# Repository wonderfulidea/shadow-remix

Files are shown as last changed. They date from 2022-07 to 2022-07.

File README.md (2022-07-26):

# Shadow Remix

Live demo at: [apps.wonderfulidea.co/shadow-remix/app/](https://apps.wonderfulidea.co/shadow-remix/app/)

- [Overview](#overview)
  - [Shadow Remix App](#shadow-remix-app)
  - [Online Gallery](#online-gallery)
  - [Gallery Admin Interface](#gallery-admin-interface)
  - [Arduino](#arduino)
  - [Repo Structure](#repo-structure)
- [Use](#use)
- [License](#license)
- [Hotkeys](#hotkeys)
- [Limitations](#limitations)
- [Parts List](#parts-list)
- [Schematics and PCB](#schematics-and-pcb)
- [Backend Setup](#backend-setup)
- [Serial Communication](#serial-communication)
- [Code](#code)
  - [Install nodejs and npm](#install-nodejs-and-npm)
  - [Compiling UI Library](#compiling-ui-library)
  - [Compiling Desktop App](#compiling-desktop-app)
  - [Adding Screensaver Animations](#adding-screensaver-animations)
  - [Compiling Gallery](#compiling-gallery)

## Overview

This project consists of a few pieces of code that interact with each other:

### Shadow Remix App

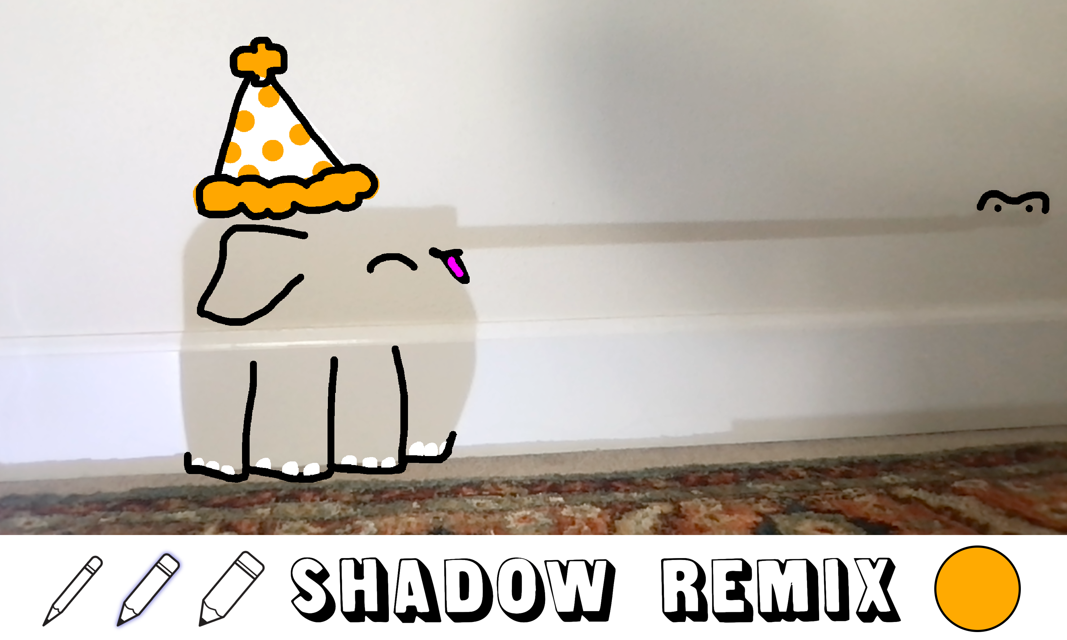
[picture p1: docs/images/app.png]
shadow remix app


The Shadow Remix drawing interface is available both as javascript code that runs in a web browser *or* as a compiled desktop app for Windows and Mac.  A live demo of the code is hosted at [apps.wonderfulidea.co/shadow-remix/app/](https://apps.wonderfulidea.co/shadow-remix/app/).

The browser-based drawing interface does not have the ability to upload photos to [our online gallery](https://apps.wonderfulidea.co/shadow-remix/gallery/) due to security issues (we don't want to let anyone on the internet upload photos to the gallery), but it does let users save images to their computers.

You will need to [compile your own copy of the desktop Shadow Remix drawing interface](#compiling-desktop-app) with credentials for editing your database.

### Online Gallery

shadow remix gallery

The gallery is a separate web app that displays approved photos drawn by visitors at the museum exhibition.  It has a feature where any new (unapproved) drawing made in the museum is shown for a brief period and then hidden until it is [approved by an admin](#gallery-admin-interface).

The gallery is currently hosted at [apps.wonderfulidea.co/shadow-remix/gallery/](https://apps.wonderfulidea.co/shadow-remix/gallery/).

### Gallery Admin Interface

shadow remix admin interface

The gallery admin interface is a private web app that displays saved photos drawn by visitors at the museum exhibition and allows an admin to approve them for public viewing.  You will need to [compile and host your own copy of the admin interface](#compiling-gallery) with credentials for editing your database.

### Arduino

The museum exhibit features a motorized shadow-making setup and a panel of button controls for easier interaction.  All the electronics for this exhibit are controlled by an [Arduino](https://www.arduino.cc/) which communicates via USB to the desktop app.

### Repo Structure

This repo consists of several subdirectories:

- [app](app) folder contains both a standalone browser-based application for shadow remix and the UI library code for connecting to a webcam, drawing to the screen, and saving images.
- [electron](electron) folder has code for compiling the desktop app with [Electron](https://www.electronjs.org/), it depends on the UI codebase located within the `app` folder.
- [gallery](gallery) folder has code for a publicly accessible gallery webpage showing images uploaded by users.
- [gallery-admin](gallery-admin) folder has code for a private admin interface for approving images.
- [arduino](arduino) folder contains arduino code for connecting hardware buttons to the app.

## Use

You need to compile your own Windows (64 and 32 bit) and Mac installers following the instructions for [compiling the desktop app](#compiling-desktop-app).  Once built, you should be able to install the app on any desktop setup.  These app is not signed and may require some additional steps to open:

- On Mac, hold down the control key and right click on the application icon, then select `Open`.  Confirm that you would like to open the application by an unidentified developer.  You should only need to do this the first time you run the application.  More info [here](https://support.apple.com/guide/mac-help/open-a-mac-app-from-an-unidentified-developer-mh40616/mac).

The first time you open the app, it will ask permission to access the webcam in a pop-up dialog.

## License

This work is distributed under an MIT license with exception to the "Lunch" font by Anthem Type.  See [Lunch Font](https://www.fontspace.com/lunch-font-f3679) for more details about licensing.

## Hotkeys

This app is primarily intended for use in a museum environment via a touchscreen and peripheral button controls.  If you have access to a keyboard or MakeyMakey, you can also use the following hotkeys:

- `ctrl/command` + `z` OR `d` to undo
- `ctrl/command` + `s` OR `a` to save image
- `backspace/delete` OR `g` to clear
- `c` brings up a dialog for selecting the webcam device
- `p` brings up a dialog for selecting the serial port (desktop app only)
- `v` saves your current drawing as an animated video (webm format).  Webm videos are large and difficult to play, but very fast to save – which is why we use them.  You can also use video editing software like Adobe Premiere to convert the video format.  Once you have the mp4s, you can [add them to the desktop app](#adding-screensaver-animations).
- `h` puts the app into screen saver mode (desktop app only).

## Limitations

- Currently, this app expects to receive webcam feeds in landscape orientation and renders out at the resolution specified in [app/src/constants.ts](app/src/constants.ts).  I've noticed that when mobile devices are in portrait mode, the returned width and height from `getUserMedia()` look like the stream is still in landscape.  I have not found a consistent way to correct this yet.

## Parts List

See [docs/Parts_List.md](docs/Parts_List.md) for a list of hardware we used for our exhibit.

## Schematics and PCB

See [docs/PCB.md](docs/PCB.md) for schematics and info about making circuit boards for the exhibit.

## Backend Setup

This app uses an AWS S3 bucket to store saved images in the cloud.  The saved images can be viewed through a webpage at [apps.wonderfulidea.co/shadow-remix/gallery/](https://apps.wonderfulidea.co/shadow-remix/gallery/).  Info about configuring the AWS Backend can be found at [docs/Backend_Setup.md](docs/Backend_Setup.md).

## Serial Communication

The serial communication protocol between the desktop app and Arduino is described in [docs/Serial_Communication.md](docs/Serial_Communication.md).  All arduino code can be found in the [arduino](arduino) folder.

## Code

### Install nodejs and npm

Before you compile any part of the code, you will need to [install nodejs and npm](https://docs.npmjs.com/downloading-and-installing-node-js-and-npm) on your machine.  All compilation steps are done through the command line.

### Compiling UI Library

This repo comes with a pre-built version of the UI library, located at [app/dist/ui.js](app/dist/ui.js).  This library should be fine as is for most cases.  **If you do not plan to modify the UI code, skip to the [next section](#compiling-desktop-app).**

If you want to change the available colors, line thicknesses, and other aspects of the UI, you can make those edits within
[app/src/constants.ts](app/src/constants.ts).

If you want to change the hotkeys, you can make those edits within
[app/src/hotkeys.ts](app/src/hotkeys.ts).

After make changes to the UI code you need to compile the `app/src/` folder to `app/dist/` using the following commands:

First, [install nodejs and npm](#install-nodejs-and-npm).

In the terminal, navigate to the `app` directory:
```sh
cd app
```

Install all dependencies:
```sh
npm install
```

Compile with [Webpack](https://webpack.js.org/):
```sh
npm run build
```

You can also start a development server at [localhost:8080/](http://localhost:8080/) using the following command:
```sh
npm run start
```

### Compiling Desktop App

The javascript code in this repo is compiled with [Electron](https://www.electronjs.org/) so that it can be run as a desktop app (rather than in a web browser).

You will need to compile your own desktop app after following the steps to [set up an AWS bucket and permissions](docs/Backend_Setup.md) and create an `.env` file with your access keys.  If make changes to the UI library in the `app` directory, you will need to [compile it first](#compiling-ui-library) before compiling a new copy of the desktop app.

If you want to change things about the app's functionality (e.g. wait time before showing the screensaver, or which buttons map to which functions) you can make those edits within
[electron/src/constants.ts](electron/src/constants.ts).

To compile for Windows and Mac:

First, [install nodejs and npm](#install-nodejs-and-npm).

In the terminal, navigate to the `electron` directory:
```sh
cd electron
```

Install all dependencies:
```sh
npm install
```

To compile for Windows and Mac:
```sh
npm run build
```

Once complete, builds are located in the `electron/build` folder.  The `shadow-remix Setup #.#.#.exe` installer should work on 32bit and 64 bit Windows machines, and the `shadow-remix-#.#.#.dmg` or `shadow-remix-#.#.#-mac.zip` files contain builds for Mac.

If you would like to compile for Linux, edit the following line in [electron/package.json](electron/package.json):

```json
"build": "npm run compile && electron-builder -mw",
```

change to:

```json
"build": "npm run compile && electron-builder -mwl",
```

Then run:

```sh
npm run build
```

Linux build has not been tested and may require additional configs, see the [electron-builder docs](https://www.electron.build/multi-platform-build.html) for more information.

If you want to make changes to the app's code, you can quickly test them by running a local development server:
```sh
npm run start
```
This will open an app window and begin running the new code automatically.

### Adding Screensaver Animations

The desktop app features a screensaver mode where you can show animations of previously drawn shadow-remixes if the station has remained inactive for a period of time.  To create the videos, draw a shadow remix and then hit the `v` key when you are done.  This will step through your entire drawing sequence and save out a video (it may be a little slow).  Using a video editor, convert the webm videos that are saved to your computer into mp4.

Next, you need to create a folder at `electron/animations/` and add several videos to this folder (with format mp4).  After making these changes you will need to recompile the app.  Alternatively, if you would like to change these videos (or add new ones) without recompiling the app, you can edit the contents of the `Resources/animations/` folder in the app's build and restart the app (on Mac, right click on the app's icon and select "Show Package Contents", on Windows right click on the app's icon and select "More > Open file location").  To be safe, use filenames without spaces for any animations you add to the app.

### Compiling Gallery

This repo comes with a pre-built version of our public gallery, located at [gallery/dist/](gallery/dist/) and currently hosted at XXXX.

In order to view your own images, you will need to recompile the gallery after [setting up your AWS bucket and permissions](docs/Backend_Setup.md) and creating a `.env` file with your access keys.

You can also edit some parameters of the gallery (e.g. how long images stay up, how often to refresh) at the top of [gallery/src/index.ts](gallery/src/index.ts).

Once complete, compile the `gallery/src/` folder to `gallery/dist/` using the following commands:

First, [install nodejs and npm](#install-nodejs-and-npm).

In the terminal, navigate to the `gallery` directory:
```sh
cd gallery
```

Install all dependencies:
```sh
npm install
```

Compile with [Webpack](https://webpack.js.org/):
```sh
npm run build
```

You can also start a development server at [localhost:8080/](http://localhost:8080/) using the following command:
```sh
npm run start
```

Note that you will also need to add `http://localhost:8080` to you list of Allowed Origins in the [AWS backend setup](https://github.com/amandaghassaei/shadow-remix/blob/main/docs/Backend_Setup.md#enable-cross-origin-requests).

Follow these same instructions to compile the gallery admin interface (located in the [gallery-admin](gallery-admin) folder).  Once compiled, the files inside [gallery-admin/dist/](gallery-admin/dist/) can be run locally or [hosted behind a password protected server](docs/Backend_Setup.md#hosting-private-admin-server) to allow admins to approve new image that are saved from the app.  **Do not post the compiled gallery-admin interface publicly because it contains your AWS secrete keys!!**  By default, all files in `gallery-admin/dist` (with the exception of index.html) should be ignored from git.

You can edit some parameters of the gallery admin interface (e.g. how often to refresh) at the top of [gallery-admin/src/index.ts](gallery-admin/src/index.ts).

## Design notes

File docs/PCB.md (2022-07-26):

# Printed Circuit Boards

This repo also includes design files for a CNC machined PCB that plugs directly into an Arduino, supports up to two motor drivers, and includes screw terminals for connecting to all switches/motors in the shadow remix station.

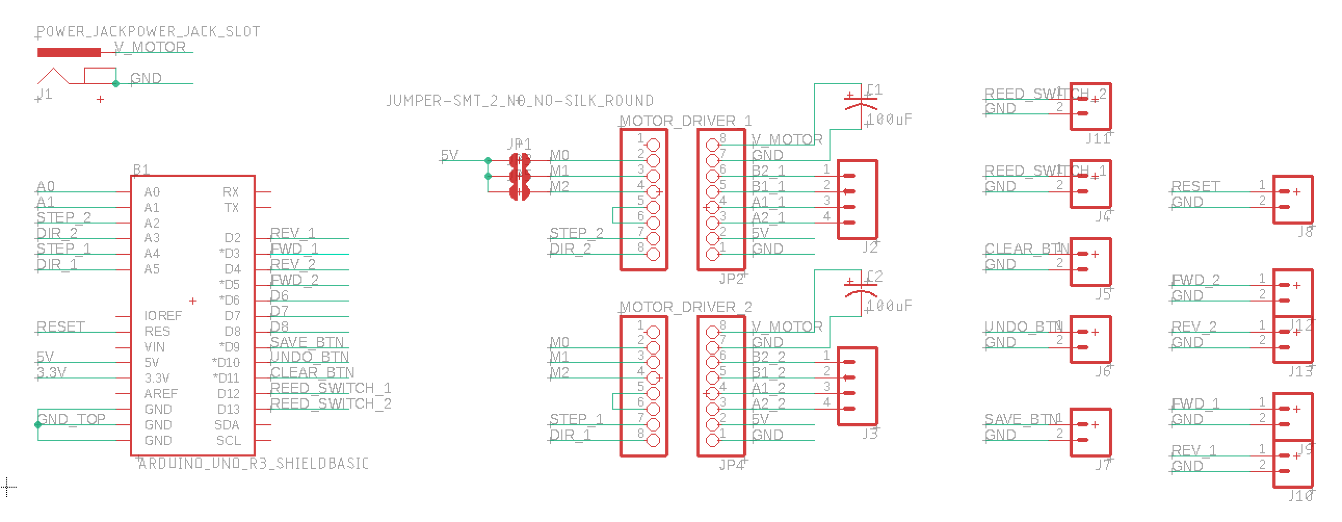
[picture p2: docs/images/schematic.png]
electronics schematic


## Wiring

See wiring diagram below:

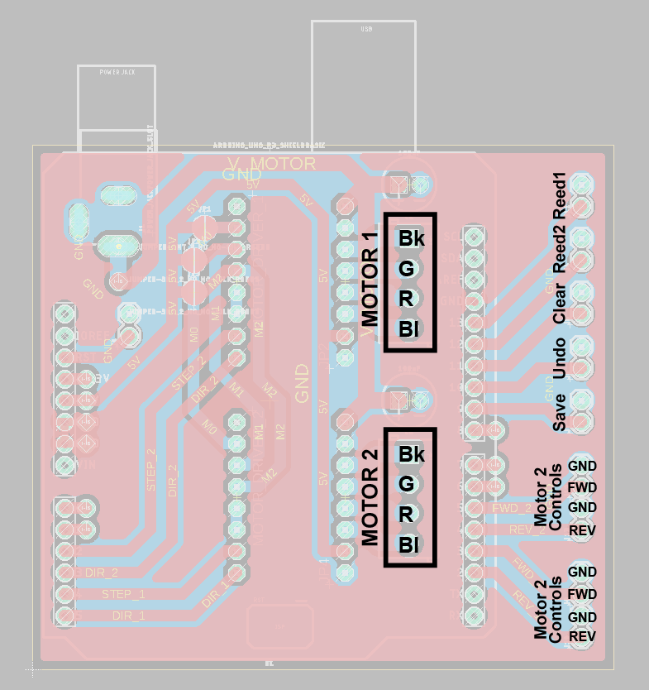
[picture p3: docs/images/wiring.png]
PCB wiring diagram


## Eagle Files

The PCB was designed in [Eagle](http://eagle.autodesk.com/) using components from the [Sparkfun](https://github.com/sparkfun/SparkFun-Eagle-Libraries) and [Adafruit](https://github.com/adafruit/Adafruit-Eagle-Library) Eagle libraries.  The design files are located in the [pcb](../pcb/) directory.

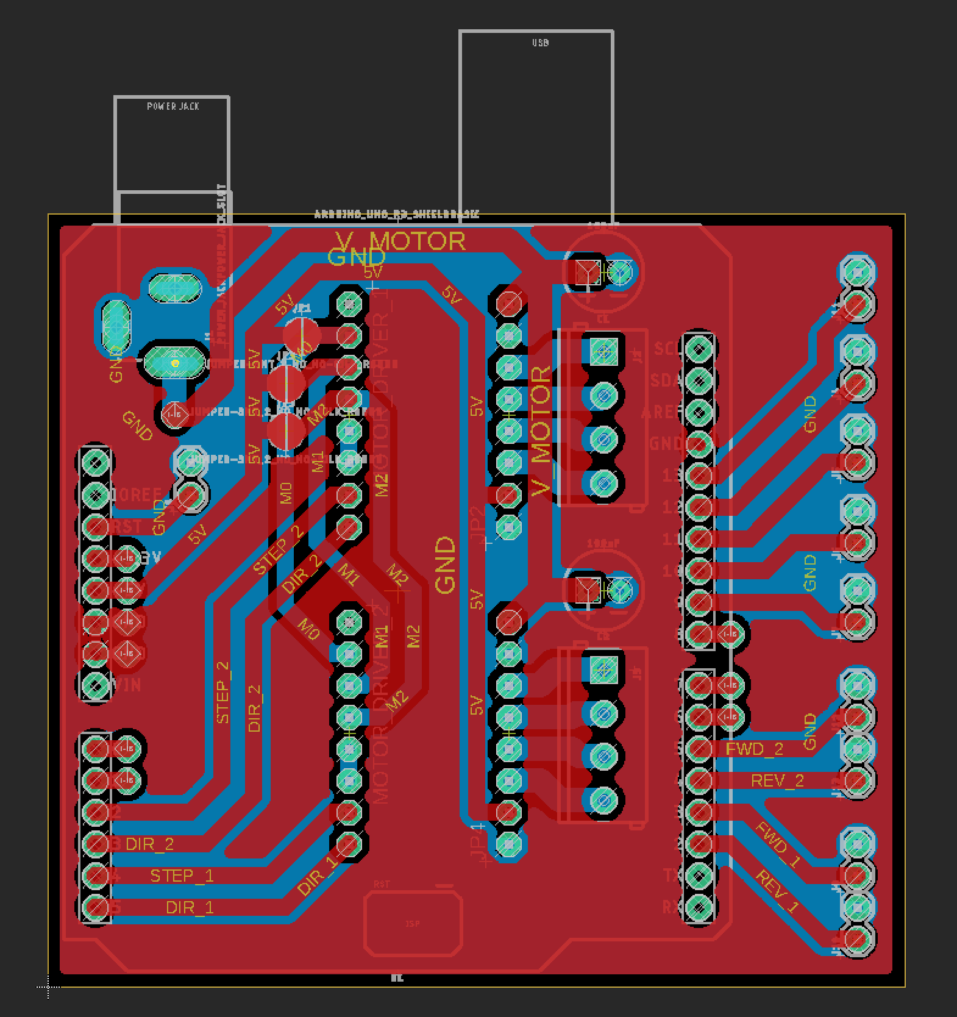
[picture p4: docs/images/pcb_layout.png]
electronics pcb layout


Features:

- Plugs directly into Arduino
- Up to two stepper motor drivers plug into PCB, supports [DRV8825](https://www.pololu.com/product/2133/pictures#lightbox-picture0J4233) and [A4988](https://www.pololu.com/product/1182/pictures#lightbox-picture0J10073) motor driver pinouts (and possibly others)
- Three solder jumpers to set stepper micro-stepping mode
- Two 100uF capacitors for smoothing power supply
- Unused Arduino IO pins have vias nearby for soldering headers later if needed
- 2.1mm jack for connecting motor power supply

Parts List:

(2x) A4988 Stepper Motor Driver [Amazon](https://www.amazon.com/HiLetgo-Stepstick-Stepper-Printer-Compatible/dp/B07BND65C8/)
(1x) through-hole male header pins 0.1" spacing [Digikey S1011EC-40-ND](https://www.digikey.com/en/products/detail/sullins-connector-solutions/PRPC040SAAN-RC/2775214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)  
(4x) through-hole female header pins 0.1" spacing [Digikey S7041-ND](https://www.digikey.com/en/products/detail/sullins-connector-solutions/PPPC081LFBN-RC/810180)  
(2x) 100uF Capacitor [Digikey 1572-1039-ND](https://www.digikey.com/en/products/detail/cornell-dubilier-illinois-capacitor/107CKE025MEM/5343969)  
(1x) 2.1mm jack through-hole [Digikey CP-002A-ND](https://www.digikey.com/en/products/detail/cui-devices/PJ-002A/96962?s=N4IgTCBcDaIMIAUC0AGFYCCSByAREAugL5A)  
(4x) 1x2 3.5mm screw terminal [Pololu 2444](https://www.pololu.com/product/2444)  
(6x) 1x2 0.1" screw terminal [Digikey A98333-ND](https://www.digikey.com/en/products/detail/te-connectivity-amp-connectors/282834-2/1150135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)  
(2x) 1x4 0.1" screw terminal [Digikey ED10563-ND](https://www.digikey.com/en/products/detail/on-shore-technology-inc/OSTVN04A150/1588864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)

## Milling PCB

Tools and Stock:

(1x) 1/64" diameter endmill [Carbide Depot CU 129974](http://www.carbidedepot.com/00156in-DIA-2FL-SE-AlTiN-164-P180142.aspx) - for cutting traces  
(1x) 1/32" dimeter endmill [Carbide Depot SGS 30398](http://www.carbidedepot.com/00312in-DIA-2FL-SE-132-AlTiN-COATED-P23340.aspx) - for cutting holes and board perimeter  
(1x) Double sided PCB blanks [Inventables 24201-06](https://www.inventables.com/technologies/circuit-board-blanks) - be sure to get FR1 blanks and not fiberglass-containing FR4  

In order to prepare the g-code for cutting the PCB, I exported the traces, holes, and board outline as PNG files from Eagle.  I made some changes to the design PNGs in Photoshop - adjustments to the hole sizes and offsets to allow enough clearance for the endmills.  The final PNGs I used are included in the [pcb](../pcb/) directory.  I used [mods.cba.mit.edu](https://mods.cba.mit.edu/) to generate gcode from the PNGs and added those to the [pcb](../pcb/) directory as well.

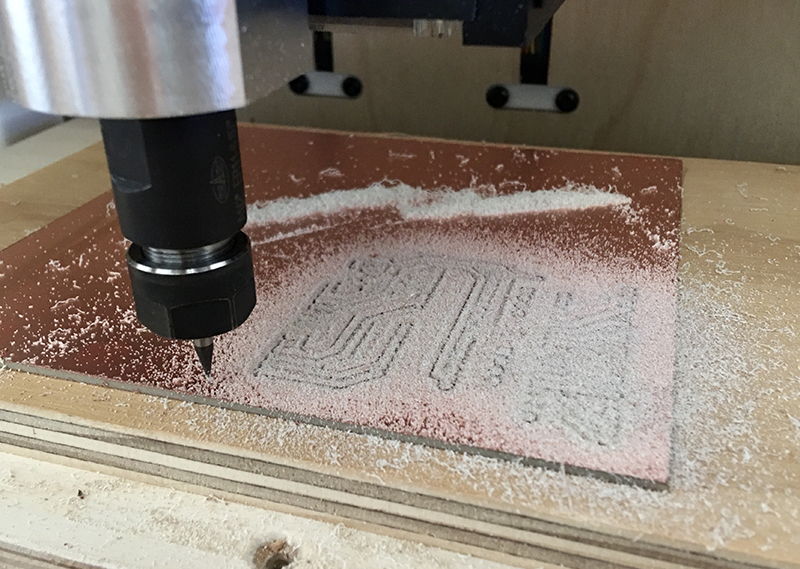
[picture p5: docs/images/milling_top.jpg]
milling trace of PCB


I used double sided tape to attach the PCB blank to a piece of spoilboard.  I zeroed to the bottom left corner of the stock and cut the holes first (1/32" endmill), then the top traces (1/64" endmill), then the outline (1/32" endmill).

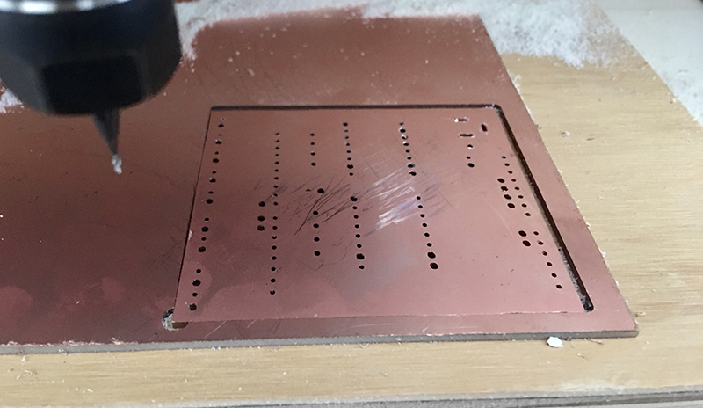
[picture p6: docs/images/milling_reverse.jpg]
aligning the reverse side of the PCB


I flipped the board and aligned it to the bottom left corner of the hole in the stock, taping it down again.  Then I re-zeroed the CNC at [-1/32", -1/32"] from the original zero to compensate for the kerf of the 1/32" outline cut.  Finally, I cut the bottom traces  with a 1/64" endmill.

I used PCB rivets to create vias through the larger holes in the PCB design:

(1x) PCB rivets 1mm ID [Botfactory](https://www.botfactory.co/shop/product/pcb-rivets-1mm-40-mil-823?category=7) or [VPC](https://www.vpcinc.com/Category/Favorit-Through-Hole-Rivets-104.cfm)

These rivets are wide enough to let a 0.1" header pin pass through, simplifying the design of the board.  Alternatively, you can use wire to create vias in your PCB, but you will need to adjust the design to move the vias away from where the headers are mounted.  I use a simple center punch and a hammer to press the rivets, rather than the suggested tools (which are quite expensive).  [More info about using PCB rivets for double-sided boards.](https://fab.cba.mit.edu/classes/863.16/doc/tutorials/PCB_Rivets/)  

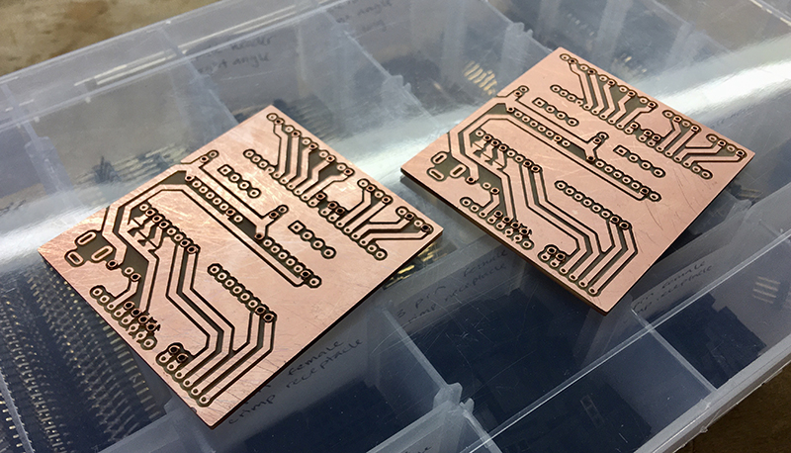
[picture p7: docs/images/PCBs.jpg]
PCBs after riveting


## Getting PCBs professionally manufactured

If you end up getting this PCB professionally manufactured, make sure that you connect the top and bottom ground planes in the design.  The current design has "GND" and a "GND_TOP" nets to make it work better for PCB milling (the nets end up getting connected by a via when the PCB is populated).  If you change the name of the GND_TOP net to GND and allow Eagle to recalculate the traces, then you should be ok for a more traditional PCB fabrication process.

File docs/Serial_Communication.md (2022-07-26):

# Serial Communication

This document describes the serial commands for communicating between the Shadow Remix desktop app and arduino.

- [Messages from Arduino to Desktop App](#messages-from-arduino-to-desktop-app)
  - [Button Pressed Commands](#button-pressed-commands)
  - [Motor Moved Commands](#motor-moved-commands)
  - [Station ID Commands](#station-id-commands)
- [Development](Development)

## Messages from Arduino to Desktop App

The arduino sends byte commands to the Desktop app to notify it of hardware interactions.  These commands have the form:

`C C D D D D D D`

The first two bits of each command give the command code (`C`) and the remaining six bits are the command data (`D`).

### Button Pressed Commands

Button pressed commands have a code of 0 and the data bits give the index (`I`) of the pressed button.  So button commands have the form:

`0 0 I I I I I I`

This format supports up to 64 (2^6) buttons.

### Motor Moved Commands

Motor moved commands are split into two bytes.  The first byte has a code of 1 and the data bits are broken up into two bits for the index (`I`) of the motor and four bits for the high bits (`H`) of the angle of the motor.  The second byte has a code of 2 and the remaining 6 bits are the low bits (`L`) of the motor angle.  So motor commands have the form:

`0 1 I I H H H H`     `1 0 L L L L L L`

This format supports up to 4 (2^2) motors with 1024 (2^10) possible angle values (the current code only uses the number 0-360 to represent position).  The high and low bits are combined to form a 10 bit number:

`H H H H L L L L L L`

### Station ID Commands

Station ID commands have a code of 3 and the data bits give the index (`I`) of the station.  So station ID commands have the form:

`1 1 I I I I I I`

This format supports up to 64 (2^6) stations.  You will need to hardcode the station ID of your station when you upload the Arduino code (default is zero).  See the Constants.h file in the Arduino code for more information.  The station ID is useful for comparing similar images taken at the same station once many images have been generated, it is not critical for basic use.

## Development

Any changes to the serial communication API should be updated in both the desktop app and the arduino code.  To make changes to the API, see [electron/src/constants.ts](../electron/src/constants.ts) and [arduino/shadow-remix/Constants.h](../arduino/shadow-remix/Constants.h).

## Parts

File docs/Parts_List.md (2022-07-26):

# Parts List

- [Arduino Uno](https://www.amazon.com/Arduino-A000066-ARDUINO-UNO-R3/dp/B008GRTSV6/) – other Arduino models will work as well, just make sure it has enough IO pins to support your setup.
- [Logitech C922x Pro Stream Webcam – Full 1080p HD Camera](https://www.amazon.com/Logitech-C922x-Pro-Stream-Webcam/dp/B01LXCDPPK/) – any webcam should work with the app.
- Touchscreen monitor
- PC/Mac computer, we used a [refurbished Mac Mini](https://www.amazon.com/Apple-MGEM2LL-LPDDR3-Desktop-Refurbished/dp/B018FD0LO8/)
- [Stepper Motor](https://www.amazon.com/STEPPERONLINE-Stepper-Bipolar-42x42x20mm-Exturder/dp/B091YDBK1S/)
- [A4988 Stepper Motor Driver](https://www.amazon.com/HiLetgo-Stepstick-Stepper-Printer-Compatible/dp/B07BND65C8/)
- [12V Power Supply](https://www.amazon.com/ALITOVE-Adapter-Converter-100-240V-5-5x2-1mm/dp/B01GEA8PQA/)

For homing the motors when the station is booted up (for consistent angle data to compare remixes with each other):
- [Reed Switch](https://www.amazon.com/BQLZR-Cylindrical-Plastic-Proximity-Magnetic/dp/B00EQ20A30) - one switch per motor.
- Small Neodymium Magnet - one magnet per reed switch.

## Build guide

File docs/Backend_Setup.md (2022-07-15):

# Backend Setup

- [AWS S3](#aws-s3)
  - [Create S3 Bucket](#create-s3-bucket)
  - [Enable Read Only Access](#enable-read-only-access)
  - [Enable Cross Origin Requests](#enable-cross-origin-requests)
  - [Setup AWS Credentials](#setup-aws-credentials)
- [Recompile Desktop App](#recompile-desktop-app)
- [Hosting Private Admin Server](#hosting-private-admin-server)

## AWS S3

S3, or Simple Storage Service, is a cloud storage service provided by Amazon Web Services (AWS). Using S3, you can host any number of files while paying for only what you use. To give you an idea of how much you will pay with this service, see the [AWS pricing page](https://aws.amazon.com/s3/pricing/):

- Storage: **$0.026 per GB**: for 10,000 250MB images, that's 7 cents per month.
- Upload: **0.0055 per 1,000 POST requests**: there is a request when the image is uploaded and another when the image is approved by an admin totalling 6 cents for 10,000 images.
- Download: **$0.09 per GB + $0.00044 per 1000 GET requests**: anytime someone views the gallery and looks at images, they are technically downloading data from AWS.  For 10,000 250MB images viewed online per month, that's 23 cents per month.
- Requests: **$0.0055 per 1000 LIST requests**:  Each time you ask the server for to refresh the gallery, you are charged for a LIST request  Refreshed once every 10 seconds, that's 8640 requests a day or $1.43 a month.  This is high enough that it makes sense to turn off this feature for a publicly available gallery website, and only have the live reloading happening in the museum setting.

This app uses an AWS S3 bucket to store saved images in the cloud.  To get started you will first need to create an AWS account at [aws.amazon.com](https://aws.amazon.com/).

### Create S3 Bucket

Once signed in search for **S3**.  You should end up at something called the S3 Console, currently located at [s3.console.aws.amazon.com/s3/](https://s3.console.aws.amazon.com/s3/):

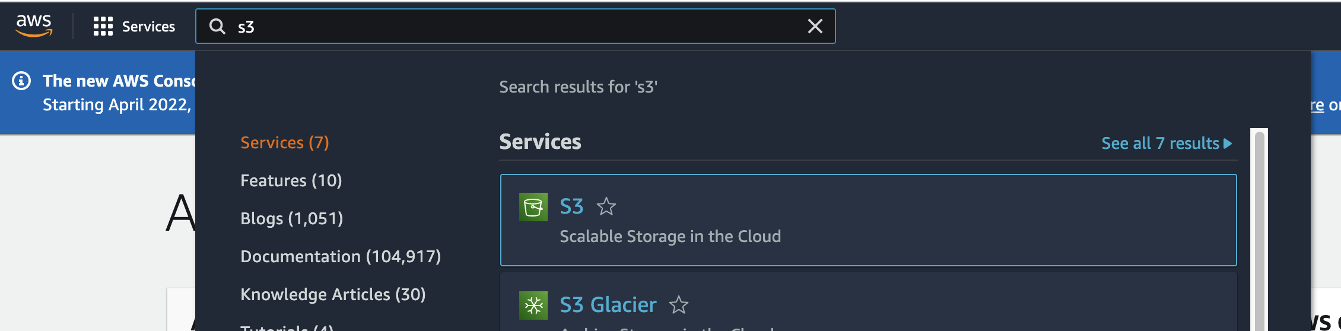
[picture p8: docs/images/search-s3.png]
search for s3 on aws


Click the button labelled `Create Bucket`:

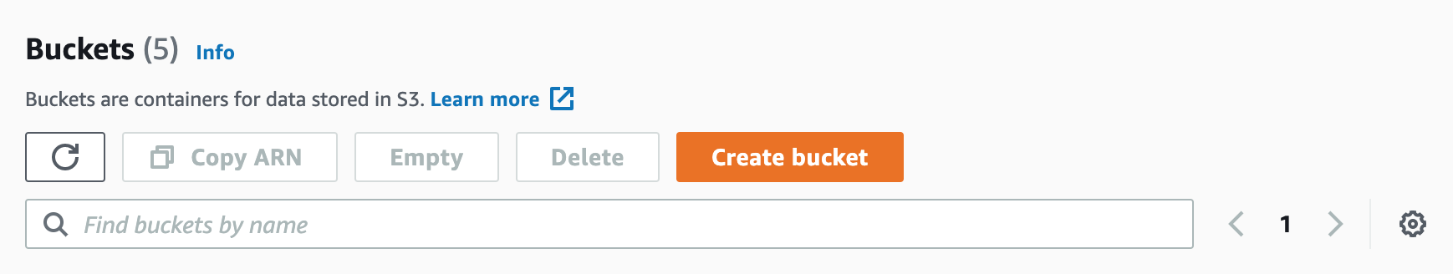
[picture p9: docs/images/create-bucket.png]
create bucket UI


Give your bucket a name and set the region to somewhere geographically close to you, I'm using `US West (N. California) us-west-1`.

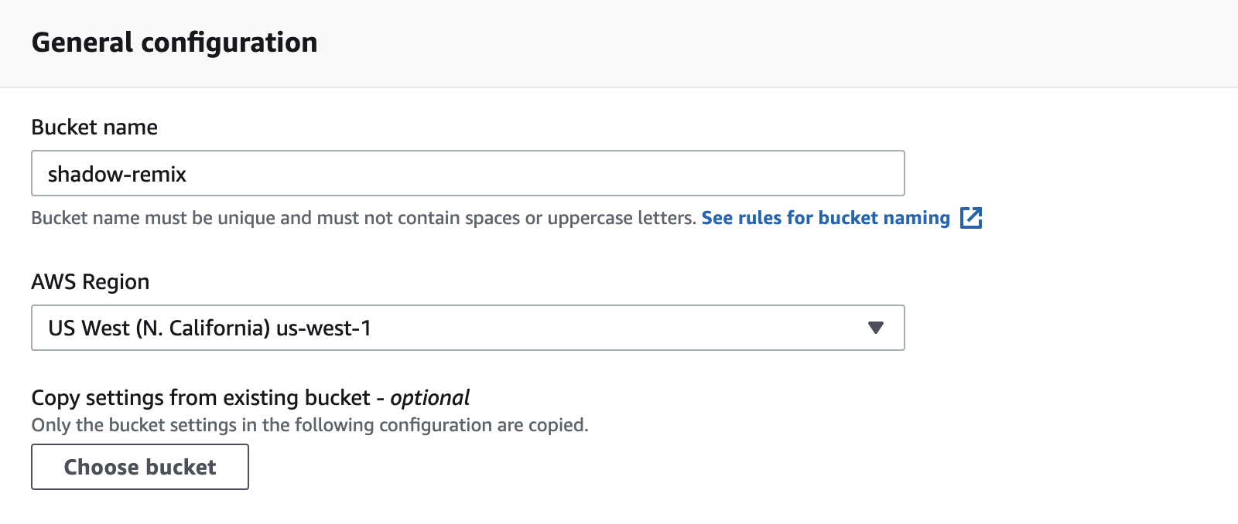
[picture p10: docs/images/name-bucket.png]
name bucket UI


Leave the remaining default settings in place and click **Create Bucket**.

### Enable Read Only Access

Select your bucket and go to the **Permissions** tab.  The default settings should say **Block public access**.  Click the **Edit** button:

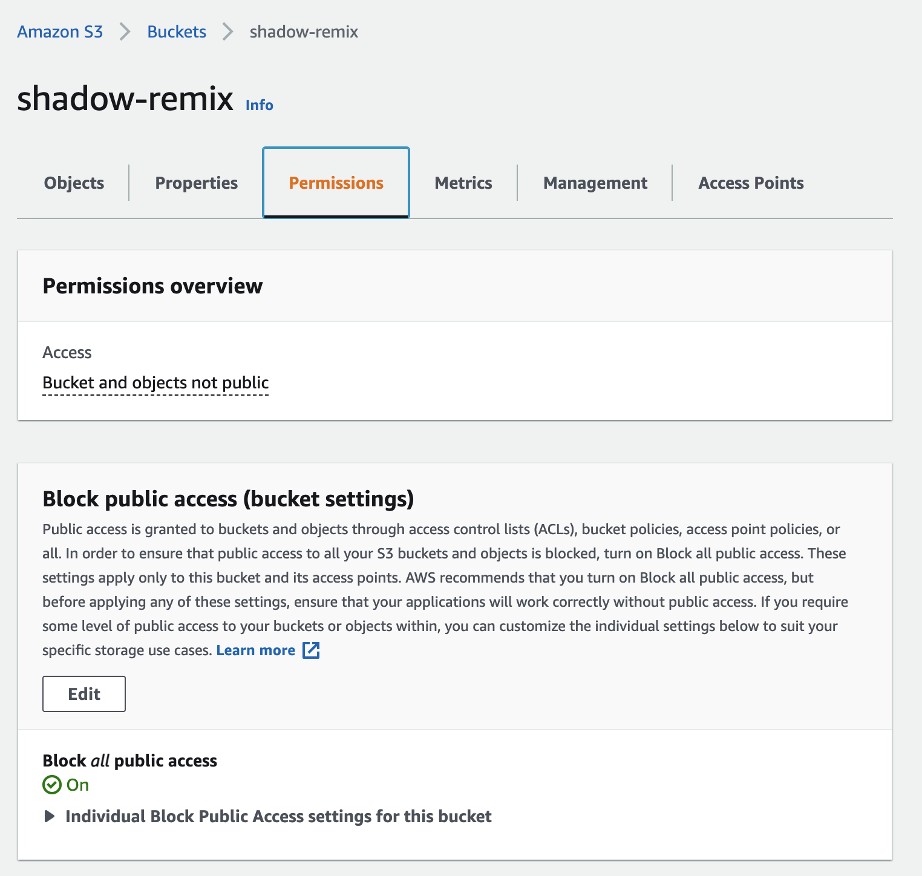
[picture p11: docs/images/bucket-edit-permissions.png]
bucket permissions UI


Deselect the checkbox to allow public access to your bucket. This will make all files inside your bucket publicly accessible over the internet.  Be sure not to upload any sensitive information to your bucket.

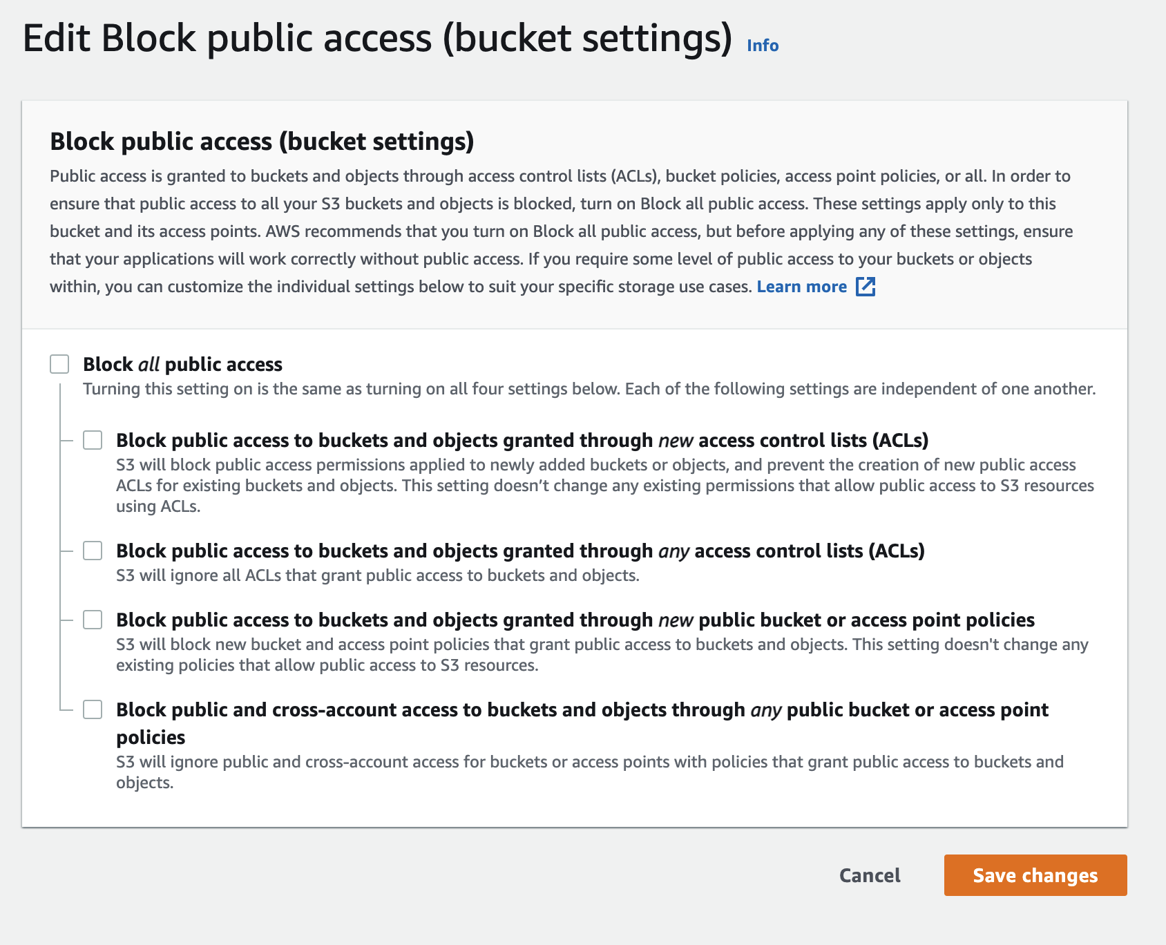
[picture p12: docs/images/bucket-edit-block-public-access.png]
bucket block public access UI


Click **Save Changes** and confirm that you would like to allow public access to the bucket.

Under **Bucket Policy** click **Edit**:

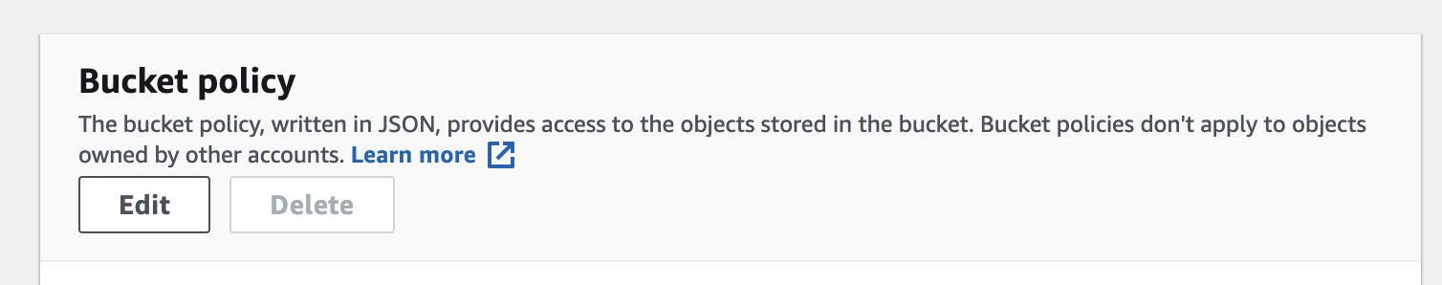
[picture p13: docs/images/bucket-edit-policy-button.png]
edit bucket policy UI


Paste the following in to the Bucket policy editor to allow read-only access to bucket contents:

```json
{
    "Version": "2012-10-17",
    "Statement": [
        {
            "Sid": "PublicReadGetObject",
            "Effect": "Allow",
            "Principal": "*",
            "Action": [
                "s3:GetObject",
                "s3:ListBucket"
            ],
            "Resource": [
                "arn:aws:s3:::Bucket-Name"
                "arn:aws:s3:::Bucket-Name/*"
            ]
        }
    ]
}
```

Be sure to edit the lines `arn:aws:s3:::Bucket-Name` and `arn:aws:s3:::Bucket-Name/*` to include your bucket name, I'm using `arn:aws:s3:::shadow-remix` for my bucket named `shadow-remix`

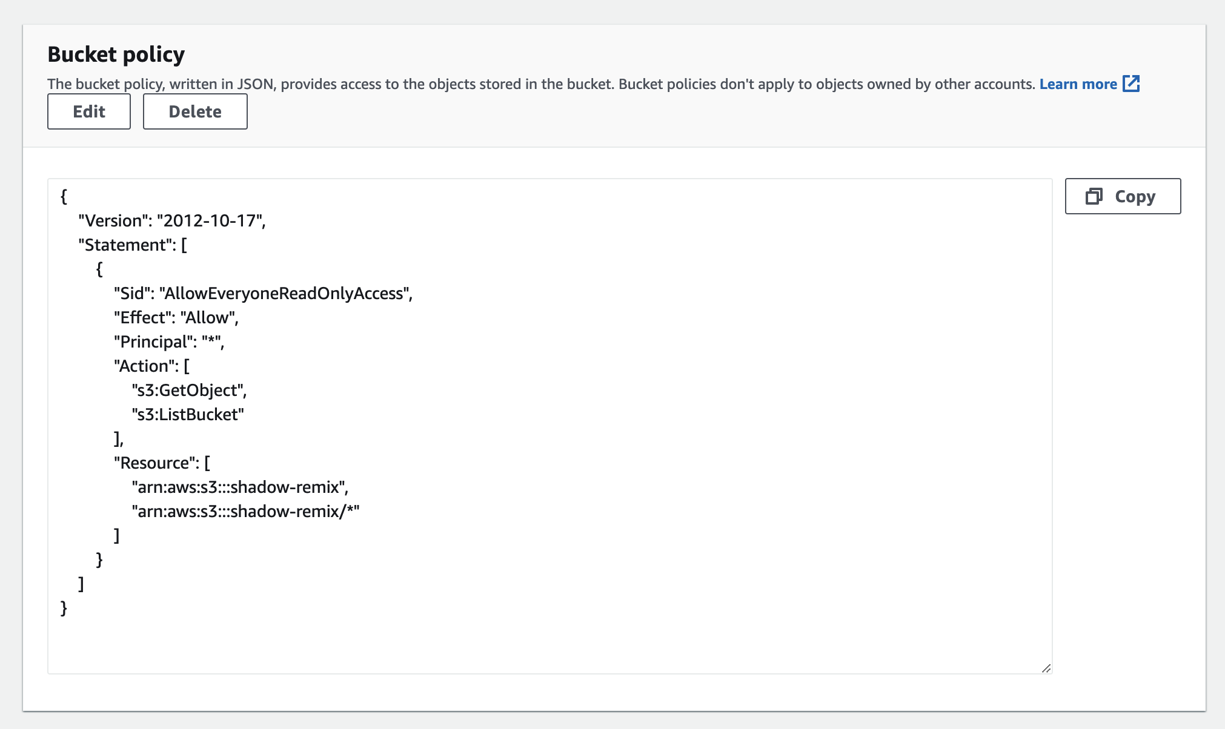
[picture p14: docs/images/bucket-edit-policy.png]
bucket policy editor


Click **Save Changes**.

### Enable Cross Origin Requests

Scrolling down further in your bucket's **Permissions** tab, find the **Cross-origin resource sharing (CORS)** section:

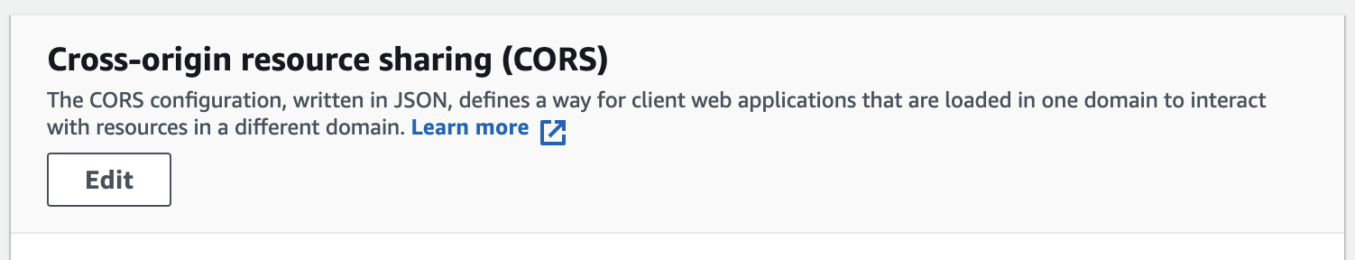
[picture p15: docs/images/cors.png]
CORS ui on awn


Click **Edit** and paste in the following:
```
[
    {
        "AllowedHeaders": [
            "*"
        ],
        "AllowedMethods": [
            "PUT",
            "GET",
            "HEAD"
        ],
        "AllowedOrigins": [
            PUT YOUR DOMAIN HERE!, e.g: "https://mydomain.com"
        ],
        "ExposeHeaders": [
            "x-amz-meta-date",
            "x-amz-meta-width",
            "x-amz-meta-height",
            "x-amz-meta-featured",
            "x-amz-meta-approved",
            "x-amz-meta-author",
            "x-amz-meta-motor-angle-1",
            "x-amz-meta-motor-angle-2",
            "x-amz-meta-station-id"
        ]
    }
]
```
You will need to update `AllowedOrigins` to contain the domain(s) where you plan to host your public image gallery and admin gallery interface (remove the comments as well).  You may leave the `AllowedOrigins` as an empty array if needed.

Click **Save Changes**.  This will allow the gallery website to access images in this bucket.

### Setup AWS Credentials

In order to upload images to AWS, we need to generate AWS Security Key Access Credentials first.  Search for Identity and Access Management (IAM) to get to the IAM dashboard, currently located at [console.aws.amazon.com/iamv2/home](console.aws.amazon.com/iamv2/home):

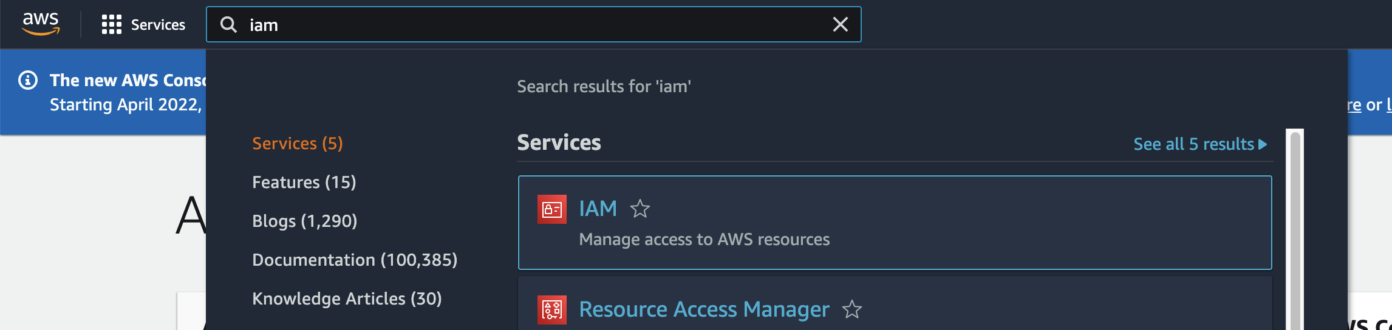
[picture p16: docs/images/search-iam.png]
search for iam on aws


In the left menu, click on **Policies** and click the **Create Policy** button:

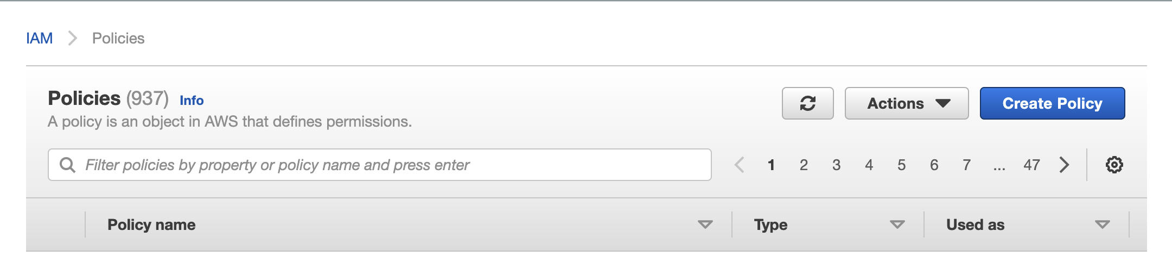
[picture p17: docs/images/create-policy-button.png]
iam policies ui


Click **Choose a Service** and select **S3** and add the following access permissions (under **Actions**):

- Write -> putObject

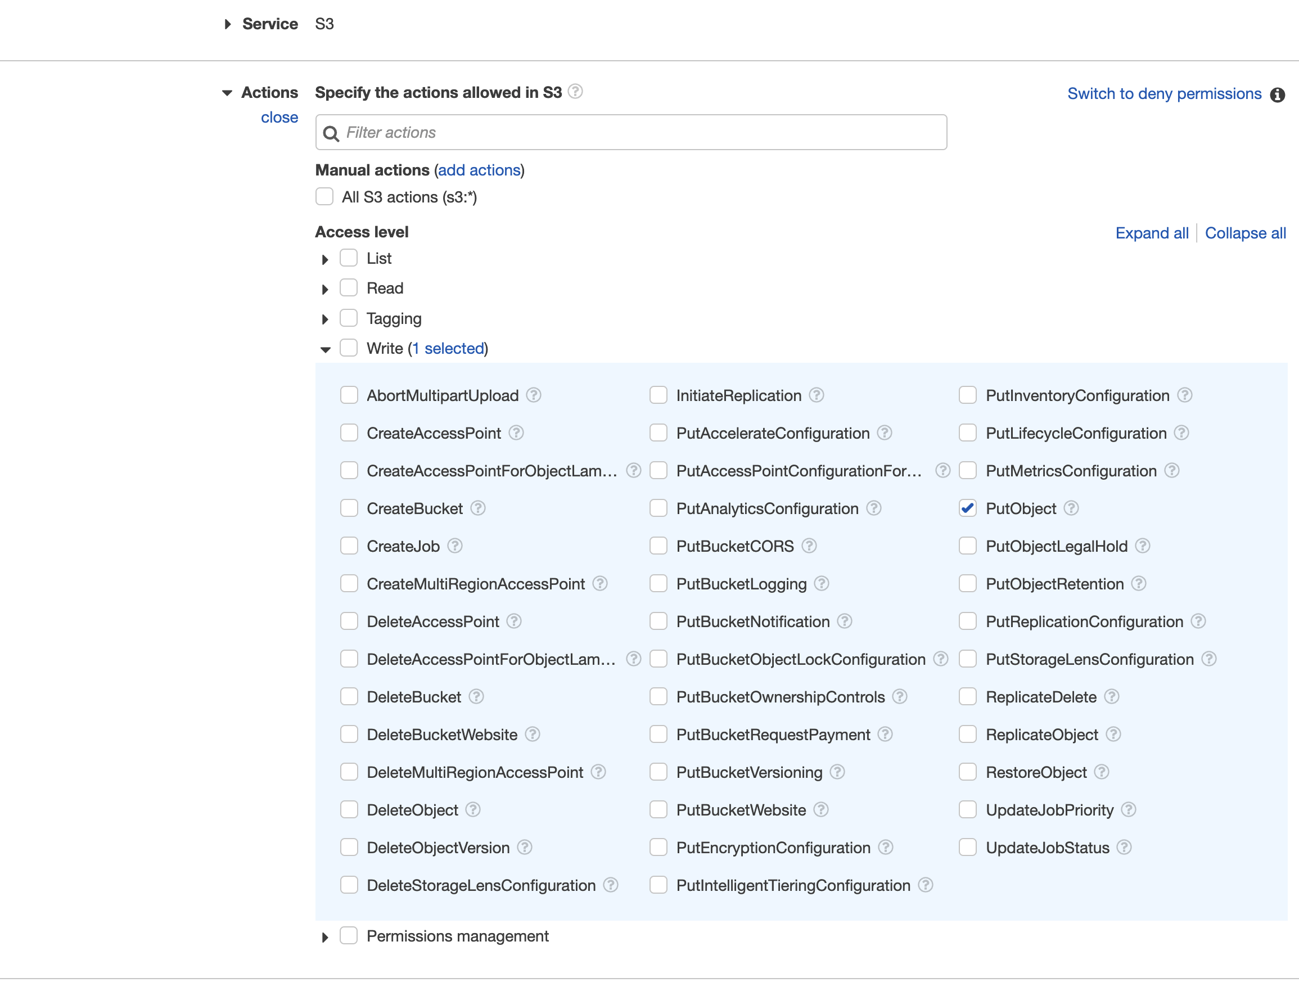
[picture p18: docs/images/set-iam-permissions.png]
set iam access permissions ui


Under **Resources** add the ARN for the S3 bucket you just created so the write permissions are restricted to your bucket.  Click **Add ARN** then type in your bucket name and select Any for **Object name**:

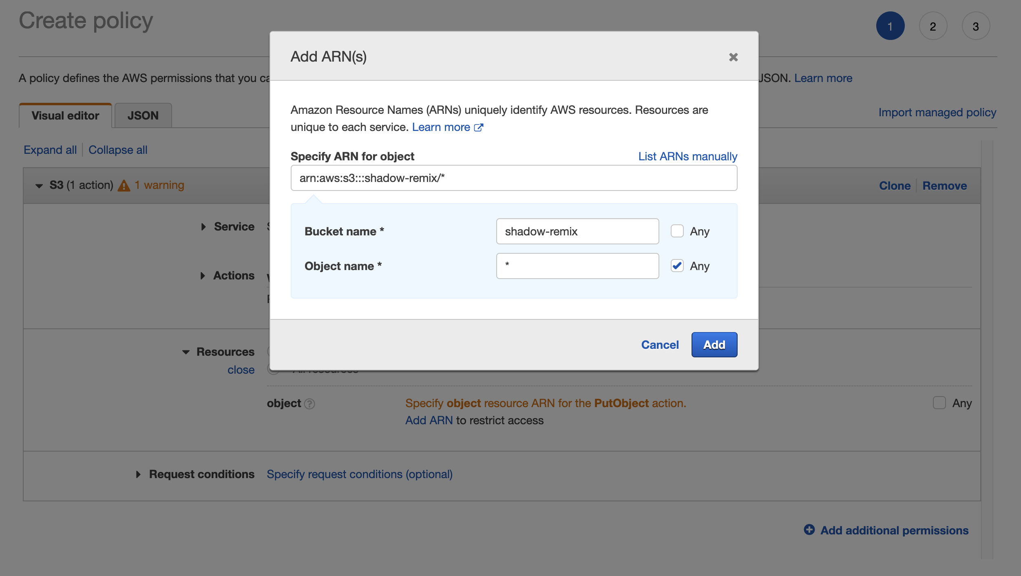
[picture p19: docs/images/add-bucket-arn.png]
add bucket arn ui


Click **Add** to add ARN.

Click **Next** until you get to the **Review Policy** step.  Give the policy a name then click **Create Policy**.  I called my policy `shadow-remix-write-objects-policy`.

Next we need to create a user to give the shadow remix desktop app access to write to our bucket.  Click on **Users** in the left menu in the IAM dashboard then select **Add users**

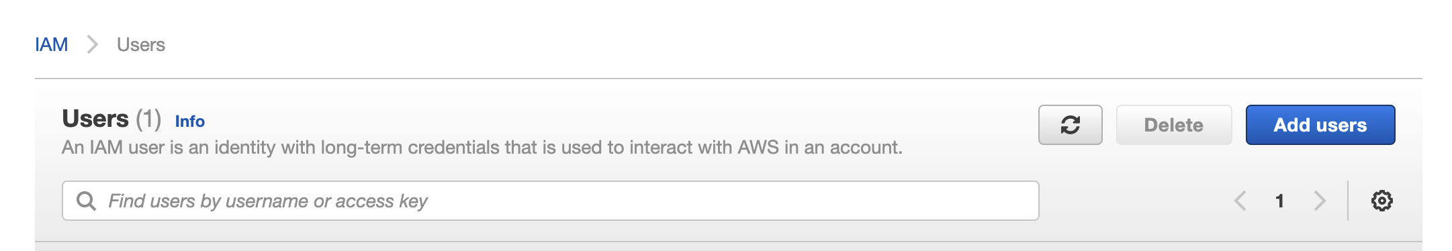
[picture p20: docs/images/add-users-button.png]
iam users ui


Give the user a name and select **Access key** for programmatic access:

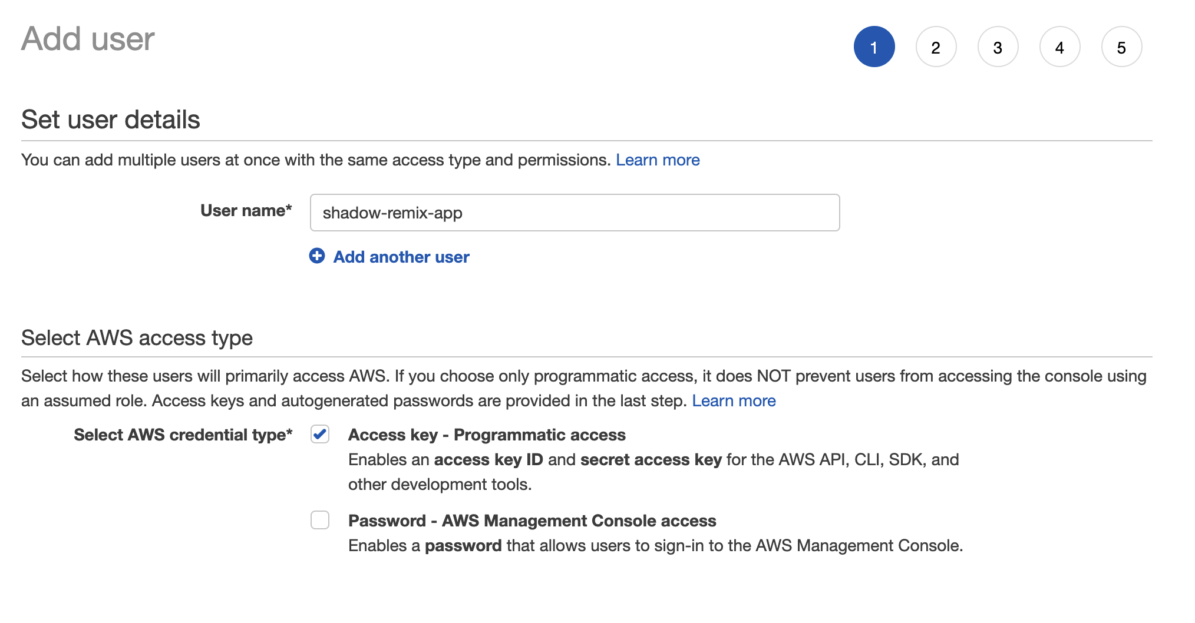
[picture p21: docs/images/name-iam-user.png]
name user ui


Next click **Attach existing policies directly** and select the policy you just created:

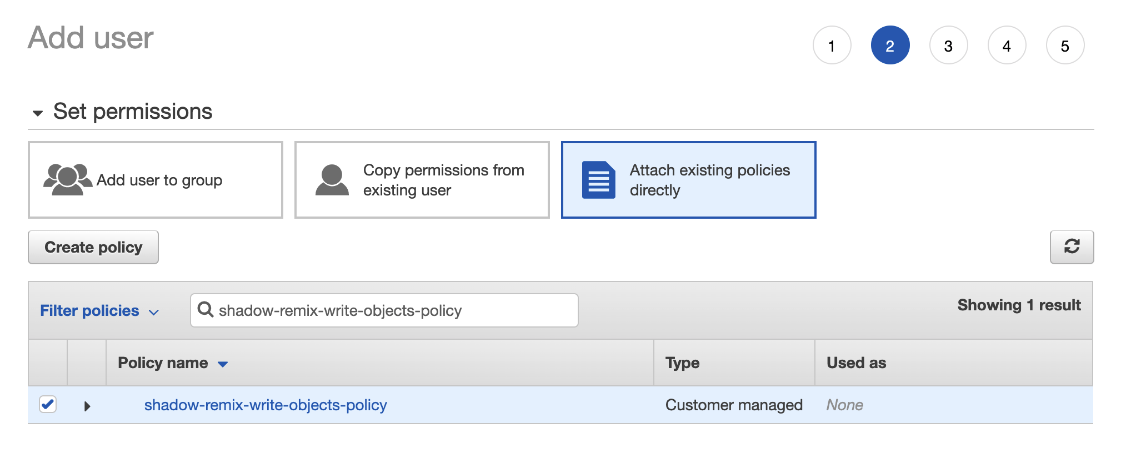
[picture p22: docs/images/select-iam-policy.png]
select iam policy ui


Click **Next** until you get to the **Review** step, then click **Create User**.  Once created, AWS will show you a screen with your access key and a secret access key.  Download this repository from Github, then create a file called `.env` in the root of the repository (the same folder where `README.md` is located), the file structure of the repository should look like this:

```
Shadow-Remix/
    arduino/
    docs/
    ....
    app/
    .env
    .gitignore
    README.md
```

Edit the `.env` file and paste in the name, region, key, and secret key for your AWS setup:

```
AWS_BUCKET_NAME=shadow-remix
AWS_BUCKET_REGION=us-west-1
AWS_ACCESS_KEY=XXXXXXXXXXXXXXXXXXXXX
AWS_SECRET_KEY=XXXXXXXXXXXXXXXXXXXXXXXXXXXXX
```

**Be careful with your secret access key, never commit it to git or share it with anyone!**  By default I've added .env files to the [.gitignore](../.gitignore), so they should not be added to git.

## Recompile Desktop App

Now that you've set up AWS and created a `.env` file, you need to recompile your desktop app so that it can use your keys and upload images to the AWS bucket.  Follow the steps outlined in the main README for [Compiling Desktop App](../README.md#compiling-desktop-app).

## Hosting a Public Image Gallery

Follow the steps outlined in the main README for [Compiling Gallery](../README.md#compiling-gallery) to recompile the image gallery app.  After recompiling, the contents of [gallery][gallery] (just index.html and the `dist` folder) can be hosted online to provide a publicly accessible gallery view of your database.  Be sure to add the domain where your gallery is hosted to the list of [cross origin "AllowedOrigins"](#enable-cross-origin-requests).

## Hosting the Shadow Remix Web App

The contents of [app][app] (just index.html and the `dist` folder) can be hosted online to provide a publicly accessible version of the shadow remix web app.  The web app will does not communicate with the server, so it does not need to be recompiled with your keys.  We are also hosting a version at [apps.wonderfulidea.co/shadow-remix/app/](https://apps.wonderfulidea.co/shadow-remix/app/).

## Hosting Private Admin Server

Follow the steps outlined in the main README for [Compiling Gallery](../README.md#compiling-gallery) to recompile the gallery admin app.  Be sure to add the domain where your admin interface will be hosted to the list of [cross origin "AllowedOrigins"](#enable-cross-origin-requests).  Because the admin gallery interface contains the private keys for accessing your AWS bucket, you **MUST** put this site behind a password in order to serve it safely.

These next steps will show you how to host a private admin server for approving new images submitted to the gallery.  This is optional, you could run the gallery admin server locally instead, but it may be easier for others on you team to access if it is hosted online.  The following steps will guide you through the process of setting this up on AWS using a combination of a few services: [S3](https://aws.amazon.com/s3/), [Cloudfront](https://aws.amazon.com/cloudfront/), and [Lambda](https://docs.aws.amazon.com/lambda/latest/dg/welcome.html).

[Create an S3 bucket](#create-s3-bucket), name it (I named mine "gallery-admin"), and set the permissions to block public access:

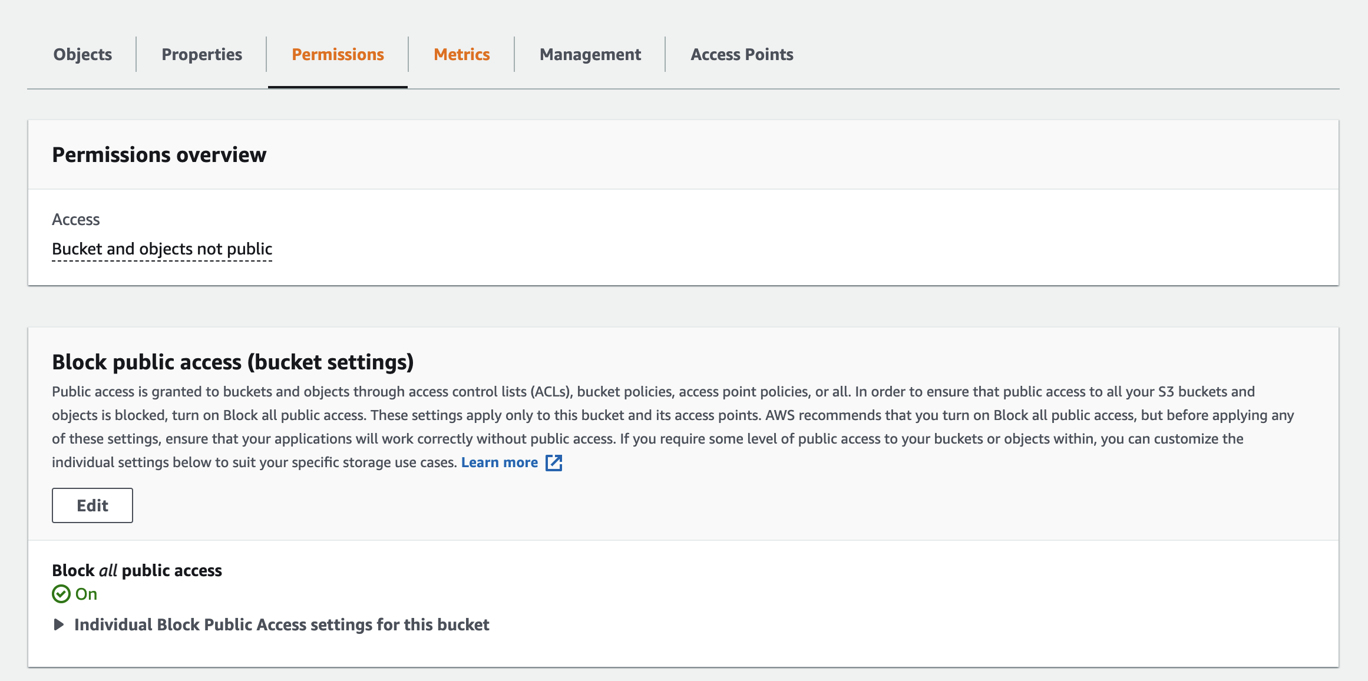
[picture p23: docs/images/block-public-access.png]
block public access to S3 bucket


For testing, upload the contents of [app/](app) (just index.html and the `dist` folder) to your bucket (we will replace this with the admin interface later).

Search for **Cloudfront** in AWS and navigate to the Cloudfront dashboard:

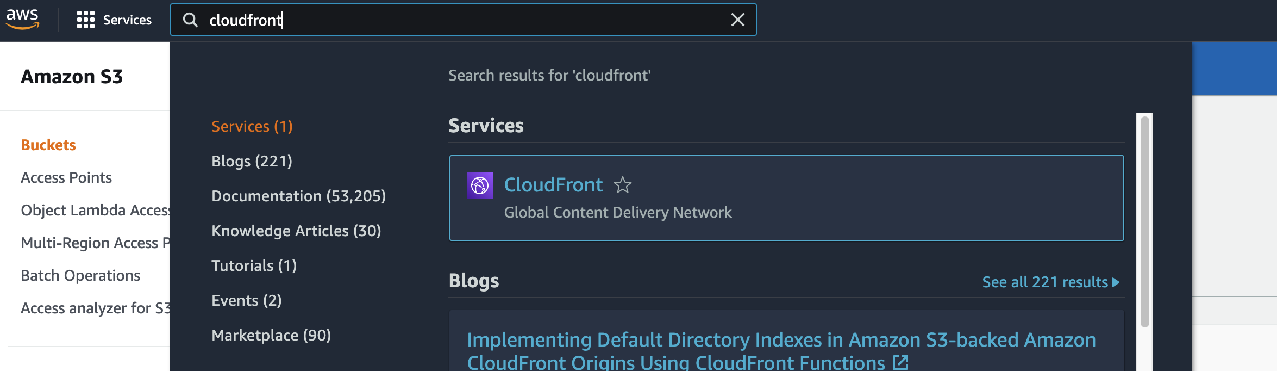
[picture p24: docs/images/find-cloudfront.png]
search for cloudfront


In the **Cloudfront** dashboard, click **Create Distribution**:

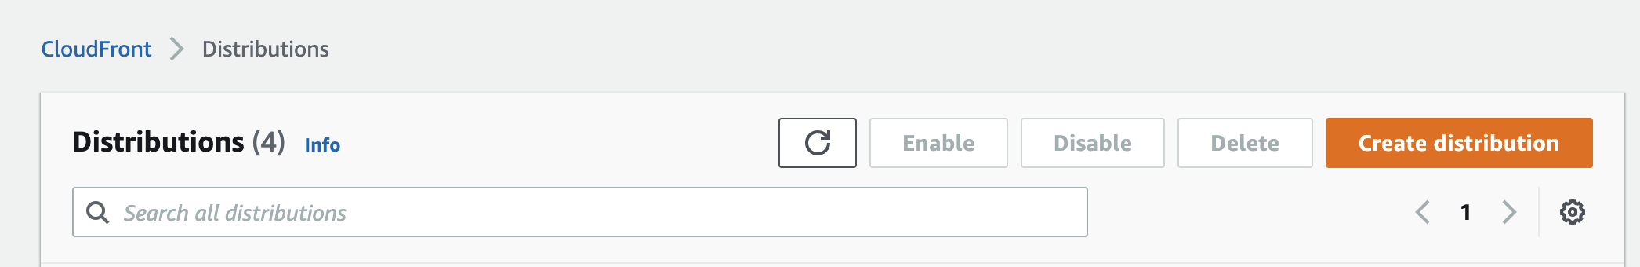
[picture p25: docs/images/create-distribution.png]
create distribution


Edit the origin domain to point to your private bucket:

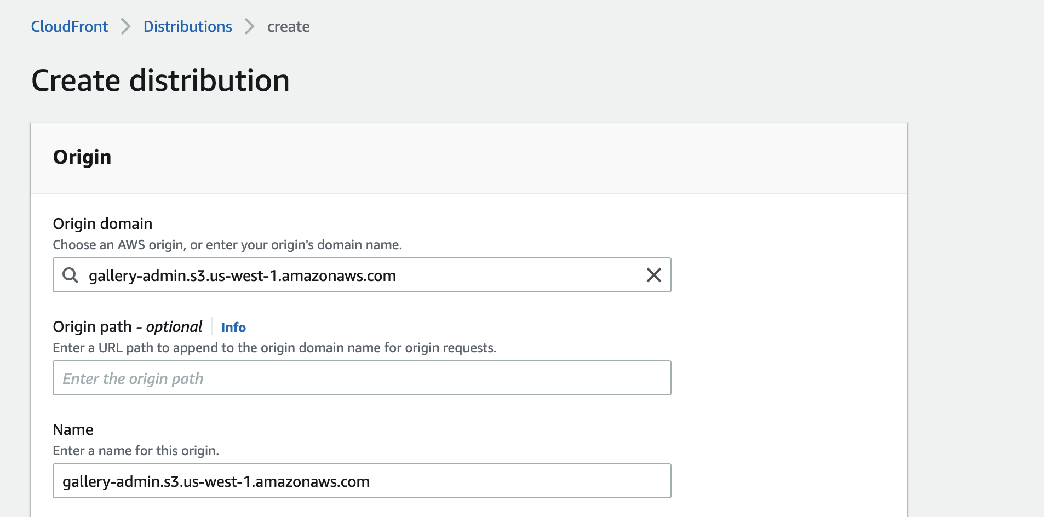
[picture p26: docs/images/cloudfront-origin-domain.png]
cloudfront origin


Under **S3 bucket access** select **Yes use OAI (bucket can restrict access to only CloudFront)** and click the button to **Create new OAI**.  Then select **Yes, update the bucket policy**.

Leave the remaining settings as they are and click **Create Distribution**.  It will take a few minutes for your distribution to be deployed; the status in the Cloudfront dashboard will read **In Progress** until then.  Anytime you make a change to Lambda or Cloudfront, you will need to wait for the Cloudfront distribution status to read **Deployed** before testing.

Now search for **Lambda** in AWS:

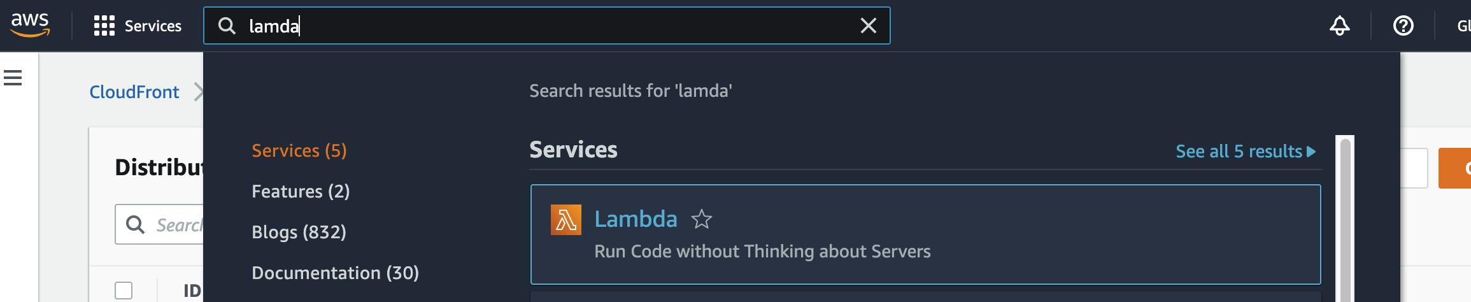
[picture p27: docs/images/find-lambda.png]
search for lambda


In the **Lambda** dashboard, switch your region to us-east-1 (N Virginia) and click **Create Function**:

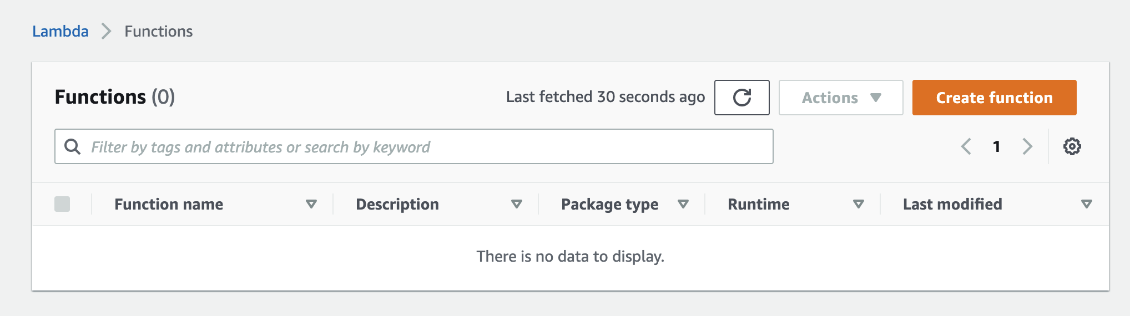
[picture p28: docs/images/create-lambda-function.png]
create lambda function


Give your function a name (I named mine "shadow-remix-admin-password") and set the **Default Execution Role** to **Create a new role from AWS policy templates** then give the role a name and select **Basic Lambda@Edge permissions (for Cloudfront trigger)**:

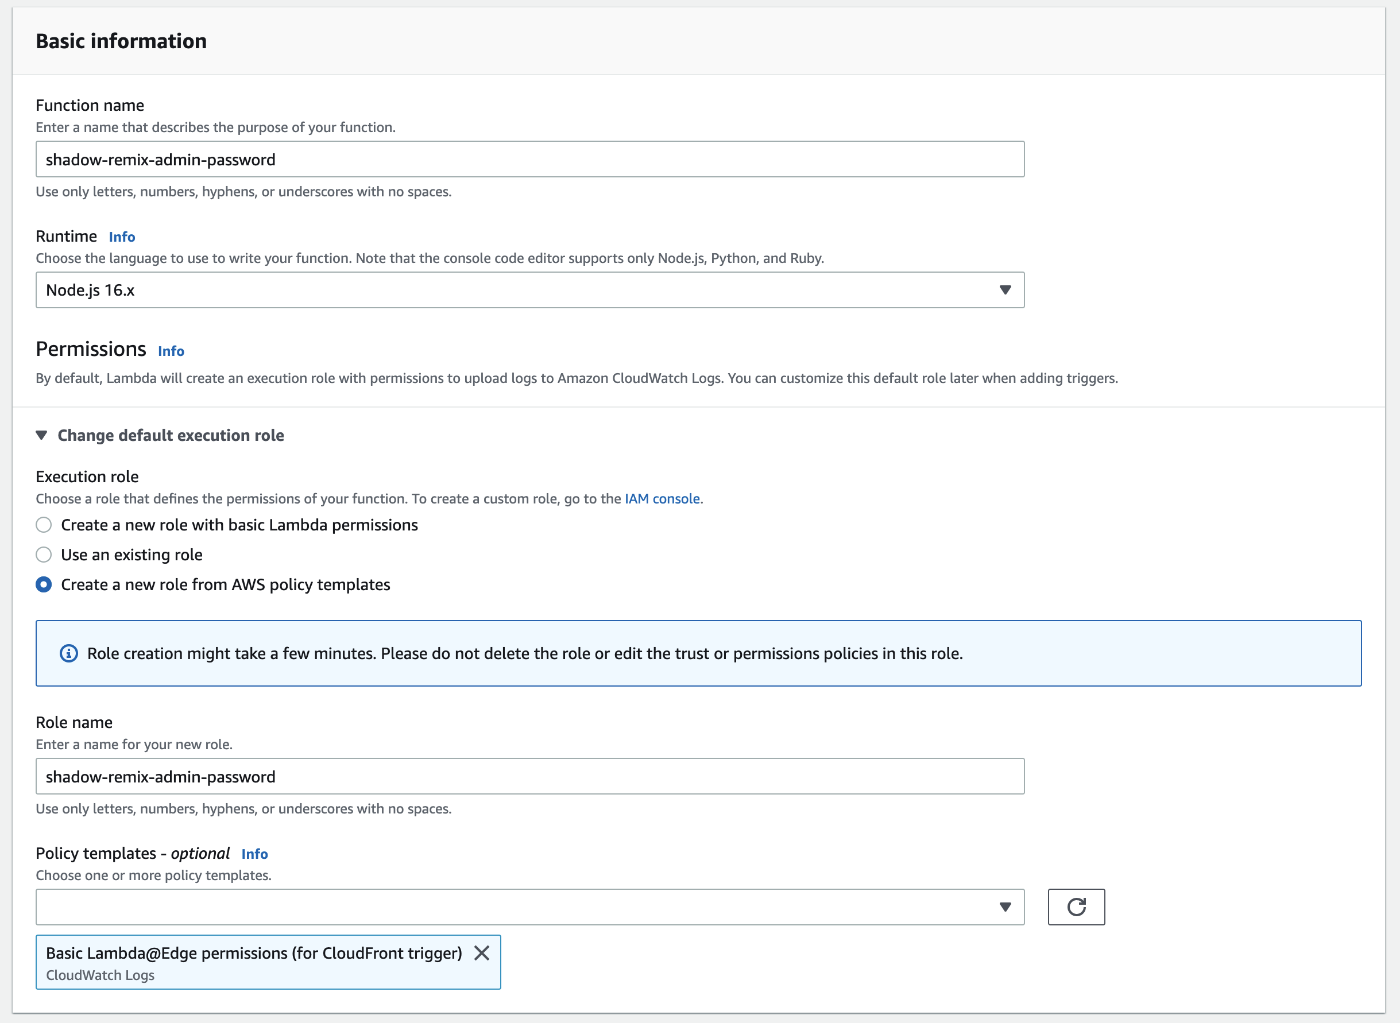
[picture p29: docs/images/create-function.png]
create function


Finally, click **Create Function**.

Paste the following code into the Lambda function (update `authUser` and `authPass`):

```js
'use strict';
exports.handler = (event, context, callback) => {

    // Get request and request headers
    const request = event.Records[0].cf.request;
    const headers = request.headers;

    // Configure authentication
    const authUser = 'user';
    const authPass = 'pass';

    // Construct the Basic Auth string
    const authString = 'Basic ' + new Buffer(authUser + ':' + authPass).toString('base64');

    // Require Basic authentication
    if (typeof headers.authorization == 'undefined' || headers.authorization[0].value != authString) {
        const body = 'Unauthorized';
        const response = {
            status: '401',
            statusDescription: 'Unauthorized',
            body: body,
            headers: {
                'www-authenticate': [{key: 'WWW-Authenticate', value:'Basic'}]
            },
        };
        callback(null, response);
    }

    // Continue request processing if authentication passed
    callback(null, request);
};
```

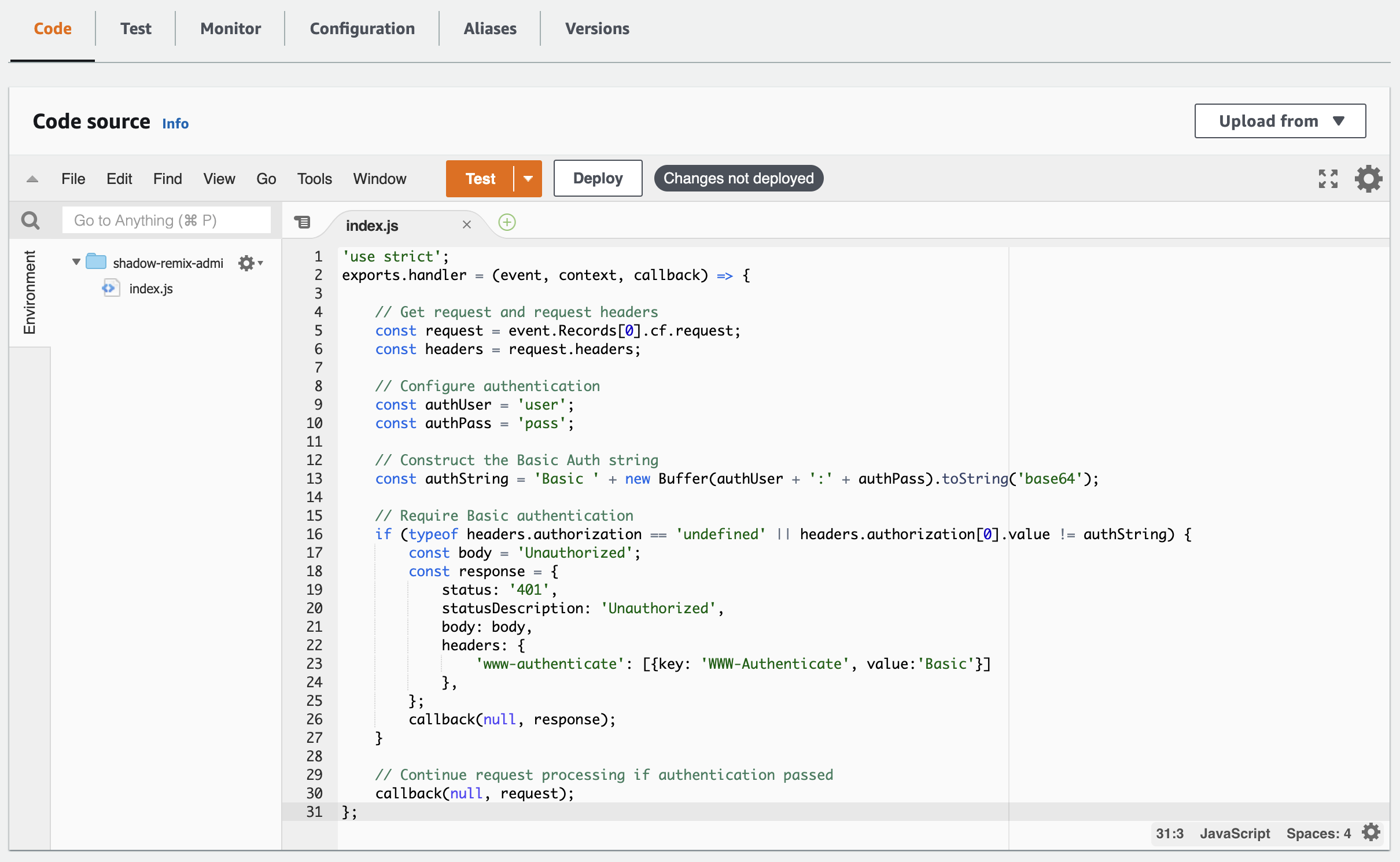
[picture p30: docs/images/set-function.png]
set function


Click **File>Save** and click **Deploy**.  Go to the **Versions**** tab and click **Publish New Version**:

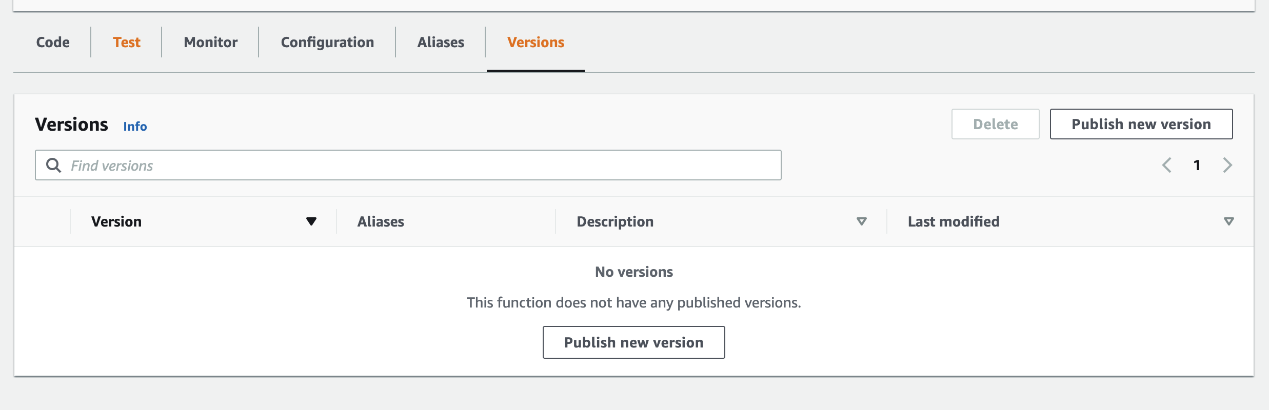
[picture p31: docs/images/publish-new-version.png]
publish new function version


Switch back to the code tab and click **Edit Code**.  At the top of the page, select **Actions>Deploy to Lambda@Edge**.  Select the Cloudfront distribution that you just set up, set the **Cloudfront event** to **Viewer request**, select **include body** and **Confirm deploy to Lambda@Edge**, then select **Deploy**.

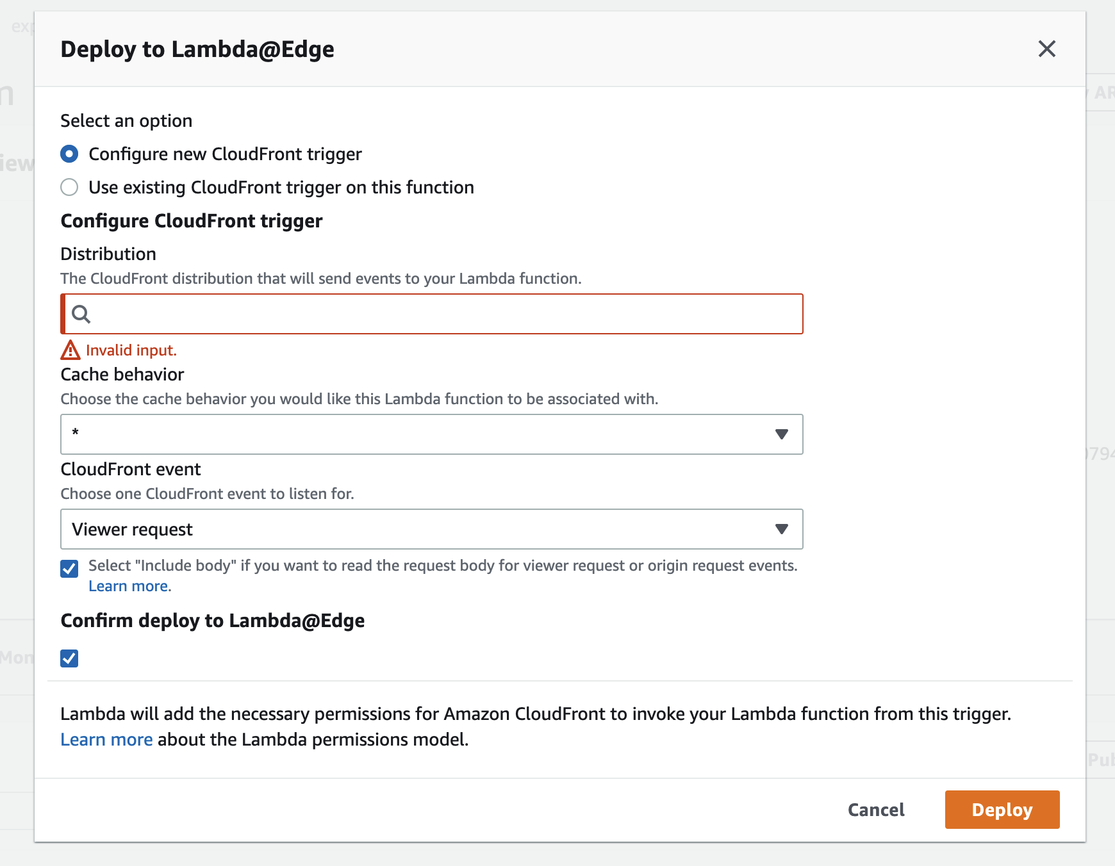
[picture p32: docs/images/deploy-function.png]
deploy function


If you navigate back to the **Cloudfront** dashboard, you will see your Cloudfront Distribution has changed back to **In Progress**.  Wait for it to change to **Deployed**.  Click on the Cloudfront distribution and copy the **Distribution domain name**:

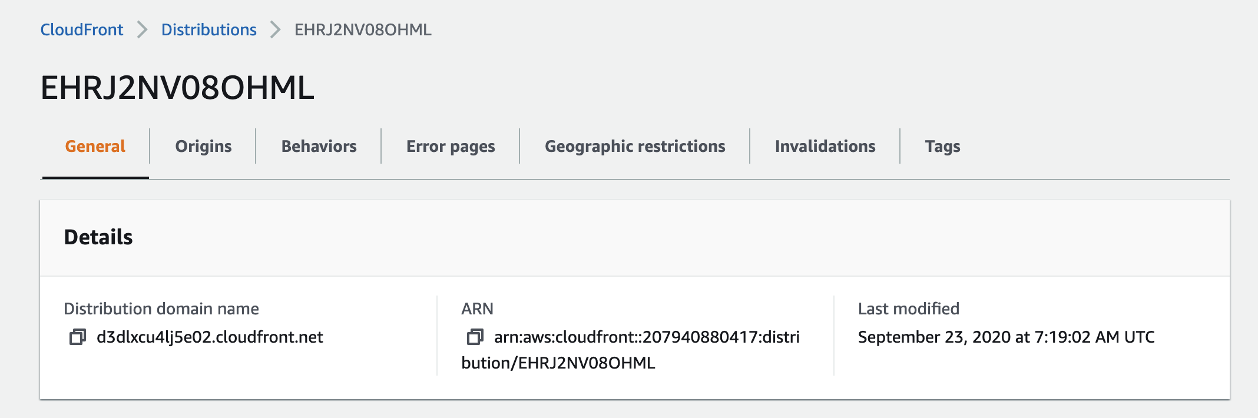
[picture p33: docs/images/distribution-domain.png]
cloudfront distribution domain


Paste this into your browser, followed with index.html.  You should see a username and password prompt:

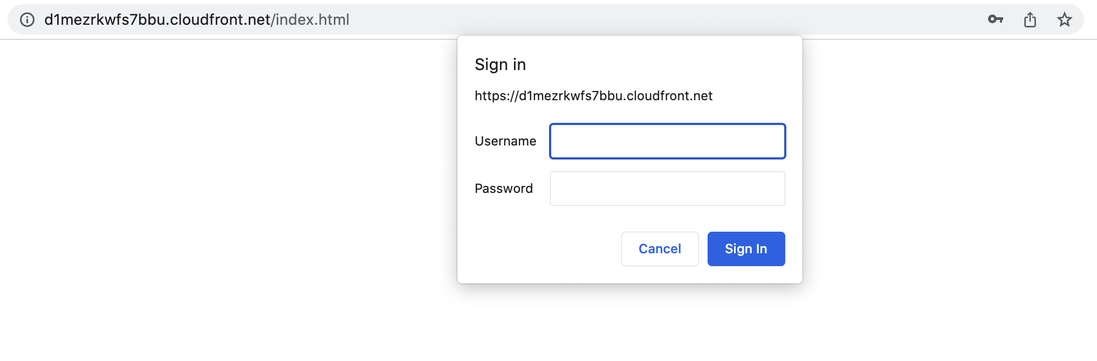
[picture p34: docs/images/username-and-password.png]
enter username and password


Enter your username and password, then you should see the shadow remix app load up.  If that is all working correctly, delete everything from your gallery-admin **S3** bucket and replace with the contents of `gallery-admin/dist/`.

Refresh the page in your browser.  If you do not see your gallery images loading up, add the Cloudfront Distribution domain from above to the list of [cross origin "AllowedOrigins"](#enable-cross-origin-requests).

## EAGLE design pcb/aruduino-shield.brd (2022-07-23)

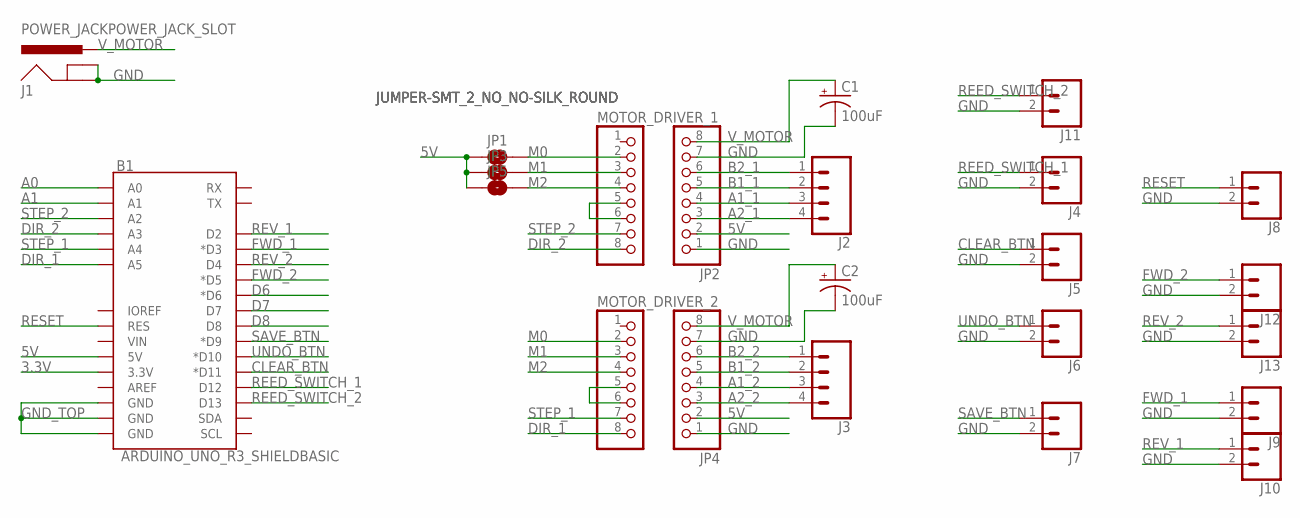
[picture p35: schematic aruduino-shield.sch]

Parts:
B1: ARDUINO_UNO_R3_SHIELDBASIC; UNO_R3_SHIELD
C1, C2: 100uF; CPOL-RADIAL-2.5MM-6.5MM
J1: POWER_JACKPOWER_JACK_SLOT; POWER_JACK_PTH_SLOT
J2, J3: CONN_04SCREW; SCREWTERMINAL-3.5MM-4
J4, J5, J6, J7, J8, J9, J10, J11, J12, J13: CONN_02; 1X02
JP1, JP3, JP5: JUMPER-SMT_2_NO_NO-SILK_ROUND; SMT-JUMPER_2_NO_NO-SILK_ROUND
JP2, JP4: PINHD-1X8CLEANBIG; 1X08-CLEANBIG
MOTOR_DRIVER_1, MOTOR_DRIVER_2: PINHD-1X8CLEANBIG; 1X08-CLEANBIG

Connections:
3.3V: B1.3.3V
5V: B1.5V, JP1.1, JP2.2, JP3.1, JP4.2, JP5.1
A0: B1.A0
A1: B1.A1
A1_1: J2.3, JP2.4
A1_2: J3.3, JP4.4
A2_1: J2.4, JP2.3
A2_2: J3.4, JP4.3
B1_1: J2.2, JP2.5
B1_2: J3.2, JP4.5
B2_1: J2.1, JP2.6
B2_2: J3.1, JP4.6
CLEAR_BTN: B1.D11 (*D11), J5.1
D6: B1.D6 (*D6)
D7: B1.D7
D8: B1.D8
DIR_1: B1.A5, MOTOR_DRIVER_2.8
DIR_2: B1.A3, MOTOR_DRIVER_1.8
FWD_1: B1.D3 (*D3), J9.1
FWD_2: B1.D5 (*D5), J12.1
GND: C1.2 (-), C2.2 (-), J1.GND, J1.GNDBREAK, J4.2, J5.2, J6.2, J7.2, J8.2, J9.2, J10.2, J11.2, J12.2, J13.2, JP2.1, JP2.7, JP4.1, JP4.7
GND_TOP: B1.GND@0 (GND), B1.GND@1 (GND), B1.GND@2 (GND)
M0: JP1.2, MOTOR_DRIVER_1.2, MOTOR_DRIVER_2.2
M1: JP3.2, MOTOR_DRIVER_1.3, MOTOR_DRIVER_2.3
M2: JP5.2, MOTOR_DRIVER_1.4, MOTOR_DRIVER_2.4
unnamed: MOTOR_DRIVER_2.5, MOTOR_DRIVER_2.6
unnamed: MOTOR_DRIVER_1.5, MOTOR_DRIVER_1.6
REED_SWITCH_1: B1.D12, J4.1
REED_SWITCH_2: B1.D13, J11.1
RESET: B1.RES, J8.1
REV_1: B1.D2, J10.1
REV_2: B1.D4, J13.1
SAVE_BTN: B1.D9 (*D9), J7.1
STEP_1: B1.A4, MOTOR_DRIVER_2.7
STEP_2: B1.A2, MOTOR_DRIVER_1.7
UNDO_BTN: B1.D10 (*D10), J6.1
V_MOTOR: C1.1 (+), C2.1 (+), J1.PWR, JP2.8, JP4.8

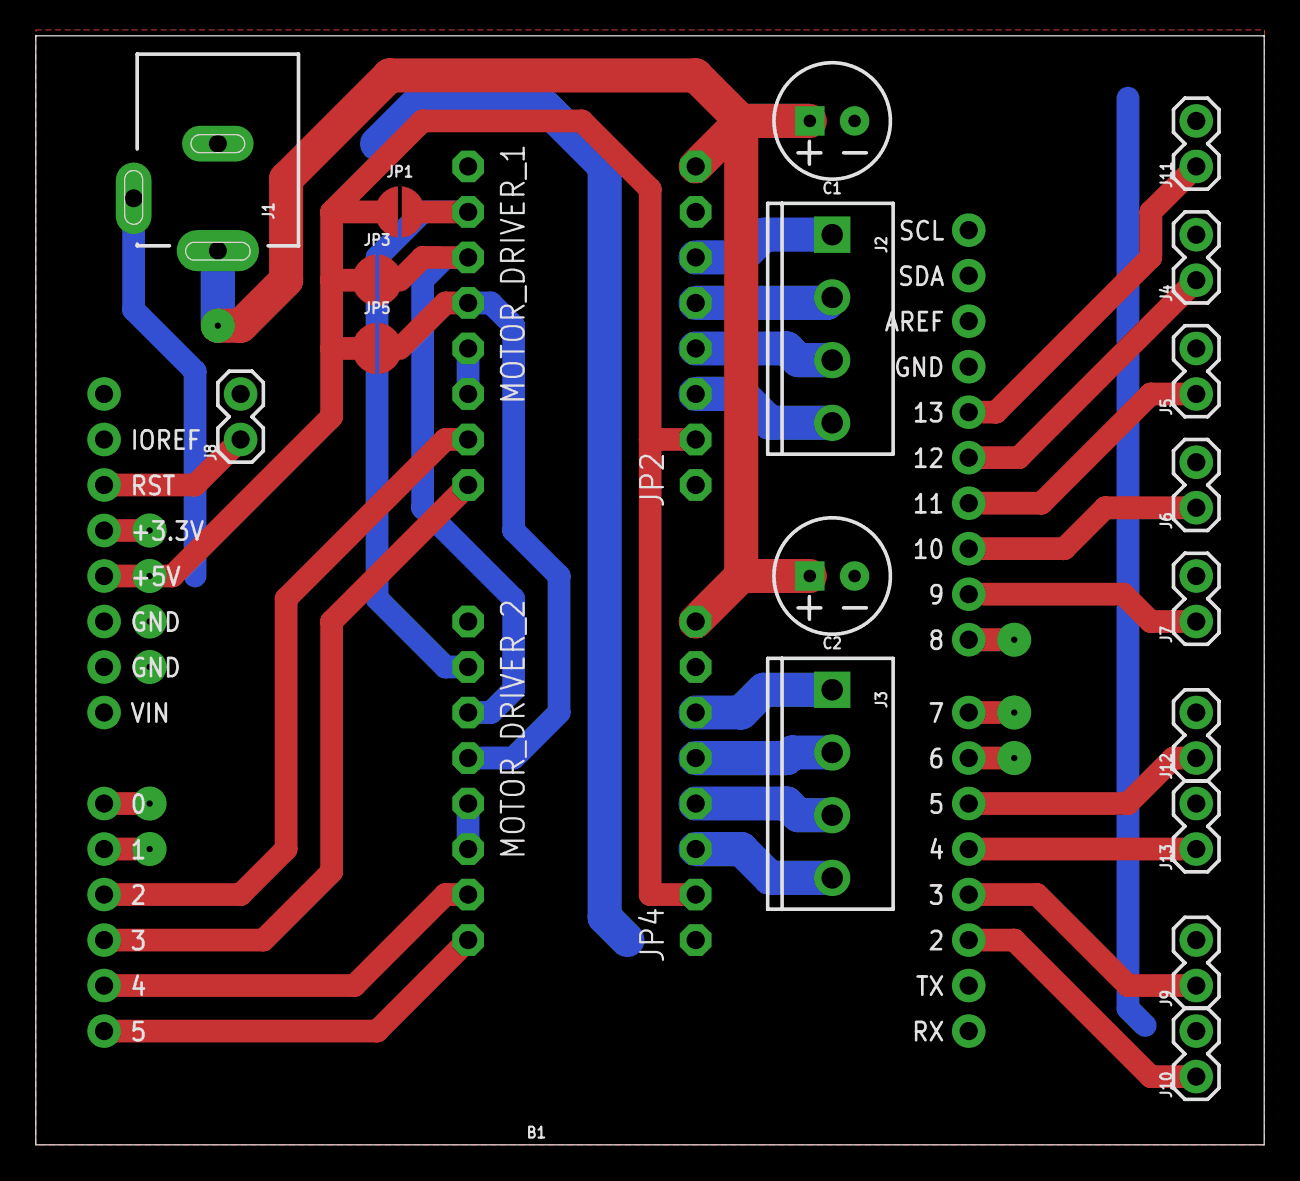
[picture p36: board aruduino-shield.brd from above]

Board: 2 copper layers, 68.6 x 61.9 mm, 23 parts (0 on the bottom side), 31 nets.

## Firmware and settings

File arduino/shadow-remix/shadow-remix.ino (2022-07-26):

#include "Constants.h"
#include "Button.h"
#include "Motor.h"

// !!!IMPORTANT!!!
// Change the STATION_ID in Constants.h before uploading.
// This will allow us to compare images that came from the same station.

// Motor config.
#define STEPPER_STEPS 200 // The number of steps on your motor.
#define RPM 10 // RPM of motor (approx).

// Define button configuration.
// Buttons should be connected to ground on one side and Arduino pin on the other.
// (Using internal pullup resistor in Arduino, no need for external current limiting resistor).
Button *buttons[] = {
  new Button(SAVE_BUTTON_INDEX, 9), // Save Button connected to digital pin 9.
  new Button(UNDO_BUTTON_INDEX, 10), // Undo Button connected to digital pin 10.
  new Button(CLEAR_BUTTON_INDEX, 11), // Clear Button connected to digital pin 11.
};

// Define motor configuration.
// Motor control switch should be connected to ground on one side and Arduino pin on the other.
// (Using internal pullup resistor in Arduino, no need for external current limiting resistor).
// DRV8825 wiring diagram: https://a.pololu-files.com/picture/0J4233.1200.png?665d623ba84232de64511d8aa6644836
Motor *motors[] = {
  // Motor(index, forwardPin, reversePin, motorDirPin, motorStepPin)
  new Motor(1, 2, 3, A5, A4, 12), // Motor (index 0) with switch connected to pins 2, 3, and motor dir/step connected to A5, A4, reed switch connected to 12.
  new Motor(0, 4, 5, A3, A2, 13), // Motor (index 1) with switch connected to pins 4, 5, and motor dir/step connected to A3, A2, reed switch connected to 13.
};

const int NUM_BUTTONS = sizeof(buttons) / sizeof(buttons[0]);
const int NUM_MOTORS = sizeof(motors) / sizeof(motors[0]);

void zero() {
  // Home motors.
  for (int i = 0; i < NUM_MOTORS; i++) {
      motors[i]->startZeroingRoutine();
  }
}

void setup() {
  // Initialize serial communication.
  Serial.begin(BAUD_RATE);
  Serial.flush();

  // Init buttons.
  for (int i = 0; i < NUM_BUTTONS; i++) {
      buttons[i]->init();
  }
  // Init motors.
  for (int i = 0; i < NUM_MOTORS; i++) {
      motors[i]->init(STEPPER_STEPS, RPM);
  }

  // Start by zeroing motors.
  zero();
}

void loop() {
  // Check buttons.
  for (int i = 0; i < NUM_BUTTONS; i++) {
      buttons[i]->update();
  }
  // Update motors.
  for (int i = 0; i < NUM_MOTORS; i++) {
      motors[i]->update();
  }
}

SIGNAL(TIMER1_COMPA_vect) {
  for (int i = 0; i < NUM_MOTORS; i++) {
      motors[i]->step();
  }
}

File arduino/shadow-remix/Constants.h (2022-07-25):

#ifndef CONSTANTS_H
#define CONSTANTS_H

// You will need to change this when uploading to different station.
#define STATION_ID 0

// IMPORTANT!!
// This file should stay in sync with /electron/src/constants.ts

// Serial communication at 9600 bits per second.
#define BAUD_RATE 9600

// Define which bits in commands correspond to what information.
#define  NUM_COMMAND_CODE_BITS 2
#define  NUM_COMMAND_DATA_BITS (8 - NUM_COMMAND_CODE_BITS)
#define  NUM_MOTOR_INDEX_BITS 2
#define  NUM_MOTOR_POSITION_BITS (NUM_COMMAND_DATA_BITS - NUM_MOTOR_INDEX_BITS)

// All command codes, range [0-3].
#define BUTTON_COMMAND_CODE 0 // Button pressed.
#define MOTOR_COMMAND_CODE_HIGH 1 // Motor moved, high bits.
#define MOTOR_COMMAND_CODE_LOW 2 // Motor moved, low bits.
#define STATION_ID_COMMAND_CODE 3 // Station ID.

// Which buttons correspond to which functions.
#define SAVE_BUTTON_INDEX 0
#define UNDO_BUTTON_INDEX 1
#define CLEAR_BUTTON_INDEX 2

#endif

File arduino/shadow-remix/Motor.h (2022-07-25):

#ifndef MOTOR_H
#define MOTOR_H

#include <Arduino.h>
#include "ButtonDebounce.h"
#include "Constants.h"

#define MAX_POSITION 360 // We are tracking 360 degrees of angular resolution.
#define SWITCH_DEBOUNCE_DELAY 100 // Number of ms to perform debounce on fwd/rev controls.
#define REED_SWITCH_DEBOUNCE_DELAY 0 // Number of ms to perform debounce on reed switch.

class Motor
{
  public:
    Motor(
      byte index,
      int forwardButtonPin,
      int reverseButtonPin,
      int dirPin,
      int stepPin,
      int reedSwitchPin
    ) {
      this->_index = index;
      this->_dirPin = dirPin;
      this->_stepPin = stepPin;
      this->_fwdBtn = new ButtonDebounce(forwardButtonPin, SWITCH_DEBOUNCE_DELAY);
      this->_revBtn = new ButtonDebounce(reverseButtonPin, SWITCH_DEBOUNCE_DELAY);
      this->_reedSwitch = new ButtonDebounce(reedSwitchPin, REED_SWITCH_DEBOUNCE_DELAY);
    }

    // Init motor, call from setup().
    void init(int steps, float rpm) {
      // TIMER 1 setup (OK if we hit this more than once).
      cli(); // Stop interrupts.
      TCCR1A = 0;
      TCCR1B = 0;
      TCNT1  = 0;
      OCR1A = int(float(16000000 / 256) / (2.0 * float(steps) * rpm / 60.0) - 1); // Must be <65536.
      TCCR1B |= (1 << WGM12);
      TCCR1B |= (1 << CS12) | (0 << CS11) | (0 << CS10);
      TIMSK1 |= (1 << OCIE1A);
      sei(); // Allow interrupts.
      
      pinMode(this->_dirPin, OUTPUT);
      pinMode(this->_stepPin, OUTPUT);
      digitalWrite(this->_stepPin, _stepPinState);
    }

    // Check button states and update motor, call from loop().
    void update() {
      if (this->_isZeroing) {
        // If in zeroing mode, drive forward until we trigger the reed switch.
        // Check if we've hit the switch.
        bool reedStateChanged = this->_reedSwitch->update();
        if (reedStateChanged && this->_zeroSteps > 180 && this->_reedSwitch->state() == LOW) {
          // Update internal motor position.
          this->_motorPosition = 0;
          // End zeroing mode.
          this->_isZeroing = false;
        }
      } else {
        bool fwdButtonChanged = this->_fwdBtn->update();
        // Button pressed when state == LOW.
        bool fwdButtonState = this->_fwdBtn->state();
        if (fwdButtonState == LOW) {
          this->_direction = HIGH;
        }
      
        bool revButtonChanged = this->_revBtn->update();
        // Button pressed when state == LOW.
        bool revButtonState = this->_revBtn->state();
        if (revButtonState == LOW) {
          this->_direction = LOW;
        }

        if (fwdButtonChanged || revButtonChanged) {
          // When starting or finishing driving motor, update position in app.
          // Only really needed on finish, but this has the secondary effect of waking up the app
          // from screensaver when motor starts to move.
          this->_writeCommand();
        }

        this->_enabled = (fwdButtonState == LOW) || (revButtonState == LOW);
      }
    }

    void step() {
      if (!this->_enabled) return;
      digitalWrite(this->_dirPin, this->_direction);
      // Toggle step pin.
      this->_stepPinState = !this->_stepPinState;
      digitalWrite(this->_stepPin, _stepPinState);
   
      // Increment motorPosition while staying in range [0, MAX_POSITION],
      int newPosition  = this->_motorPosition + (this->_direction ? 1 : -1);
      if (newPosition > MAX_POSITION) {
        newPosition = 0;
      } else if (newPosition < 0) {
        newPosition = MAX_POSITION;
      }
      this->_motorPosition = newPosition;
      if (this->_isZeroing) {
        this->_zeroSteps += 1;
      }
    }

    void startZeroingRoutine() {
      this->_zeroSteps = 0;
      this->_isZeroing = true;
      // Drive motors forward until reed sensor is triggered.
      // This routine is picked up in update() function.
      this->_direction = HIGH;
      this->_enabled = true;
    }
   
  private:
    // Motor index in serial commands (range 0-4).
    byte _index;
    // Motor state.
    volatile int _motorPosition = 0;
    // Stepper connections.
    int _dirPin;
    int _stepPin;
    // Stepper state.
    bool _enabled = false;
    bool _direction = HIGH; // HIGH is forward, LOW is reverse.
    volatile bool _stepPinState = LOW;
    // Flag to signal zeroing mode.
    bool _isZeroing = false;
    int _zeroSteps = 0; // Ensure that we rotate at least a half revolution during zero routine.
    ButtonDebounce *_reedSwitch;
  
    // Button instances.
    ButtonDebounce *_fwdBtn;
    ButtonDebounce *_revBtn;

    void _writeCommand() {
      byte dataMask = ((1 << NUM_COMMAND_DATA_BITS) - 1);
      Serial.write(MOTOR_COMMAND_CODE_HIGH << NUM_COMMAND_DATA_BITS | this->_index << NUM_MOTOR_POSITION_BITS | (this->_motorPosition >> NUM_COMMAND_DATA_BITS) & dataMask);
      Serial.write(MOTOR_COMMAND_CODE_LOW << NUM_COMMAND_DATA_BITS | this->_motorPosition & dataMask);
    }
};

#endif

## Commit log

2022-07-23 small fixes
    [aruduino-shield.brd, aruduino-shield.sch]
2022-07-26 wiring diagram

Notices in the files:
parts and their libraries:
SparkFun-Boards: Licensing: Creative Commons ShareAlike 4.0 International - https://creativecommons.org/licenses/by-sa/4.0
